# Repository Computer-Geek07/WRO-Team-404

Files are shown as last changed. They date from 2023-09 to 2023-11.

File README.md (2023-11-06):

# Introduction to the team
We are Team 404, a group of three tenth graders from Dhirubhai Ambani International School who are interested in robotics and innovation. We have different roles and skills in our team:

**Arjun**: He is one of our programmers, who works mainly with PID and control algorithms when it comes to the bot. He designed most of the algorithms that go into integrating the sensor feedback and making our bot work precisely as it should.

**Atishaya**: He is another programmer, who works with Arjun to develop and test the robot’s software. He however, focusses mainly on aspects like low-level communication. He worked very hard on the initial code for the open and obstacle categories.

**Meher**: She is our constructor, who designed the mechanical systems of the bot. She specialises in Computer Aided Drawing but managed quite well with the practical construction aspects as well.

# Engineering process

### Programming and electricals
Initially, we were hoping to design our bot, completely devoid of any form of computer vision, relying on a network of colour and proximity sensors for both the open and obstacle categories. However, we very quickly realised that this was if not impossible then at least extremely impractical and switched to a raspberry pi based computer vision system. We looked into various systems and combinations of systems, including ROS to simplify the developmoent process and OpenCV or YOLO or even training our own model for the detection of the traffic signs. Eventually we settled on a combination of ROS to handle hardware coordination and OpenCV to handle object detection. Our openCV program involved masking the image to only read red and green and then running Canny edge detection followed by contour detection to find the traffic signs. Once the traffic signs were found, we would once again run a colour mask to find out whether they were red or green.

We quickly discovered that this process was not only quite difficult to program but it also caused the raspberry pi to become a massive computational bottleneck, slowing down our bot and making it extremely unreliable at high speeds. Looking into alternatives, we discovered HuskyLens, a device designed by DFRobot, that was built to solve exactly the problem we are facing. Switching to the HuskyLens, we added an arduino for low-level hardware communication and for controlling the motors. To this we added an l298N to control our DC motor alongside a DS 35kgcm servo. We also added an MPU6050 and ultrasonics which alongside a PID algorithm helped keep the bot centred on the track and prevent accidents.

After our nationals, we chose to further redesign our bot, we replaced the Arduino Uno with an Arduino Nano Esp32, a smaller and faster board. We also replaced the unreliable HC-SR04s with far more reliable analog ultrasonics from DFRobot, the URM-09s. We also added an ultrasonic in the front of the bot for the obstacle challenge round, where exiting each turn near the centre of the track was of the utmost importance. Our open code was very similar to before, utilizing nearly the same PID algorithm. We were however, forced to completely redesign our obstacle algorithm as it had proven to be unreliable and faulty during the nationals. 

## Construction
While preparing for Nationals, we explored various mechanisms like Ackerman Steering in CAD but eventually decided that most of these were too elaborate for our needs. Our first constructed chassis consisted of a mobile front axle. The wheels were attached to two pivoting parts on either side, which were connected by a servo-controlled link. Our rear axle was fixed and the driving axle in this design. This iteration was bulky and a sharper turn than 35 degrees was practically unfeasible without major slipping which would hinder readings, especially for the IMU. This setup produced an ICR (Instantaneous centre of rotation) and turning radius far too large to fit within the 1m box and made turning a challenge. 

To create a smaller turning radius, we decided to implement all-wheel steering in our next design. We connected our servo to the front and back axles, which were independent of the chassis frame with gears and links. Thus, both front and back axles turned at the same time, in opposite directions, giving the desired narrow ICR. Unfortunately, after extensive testing, we concluded that gear play caused the axles to turn at different angles causing drifting. In the end, our final Nationals robot was front-wheel driven and rear-wheel steering, an alternative that gave us the least slippage and drift.

After the nationals were over, we reworked our bot, using our learning from the nationals to create a simpler, more elegant and far more precise bot.

# Programming

## Open category
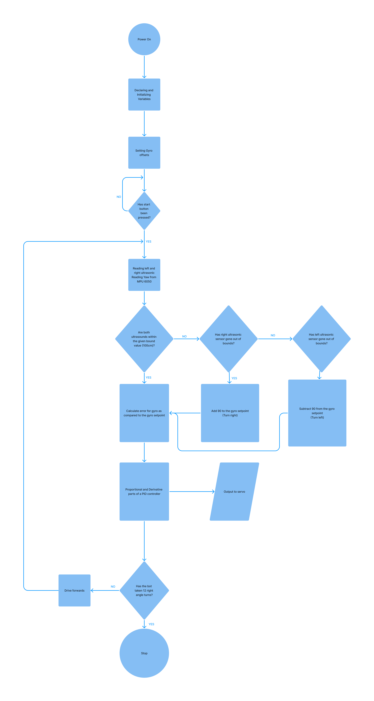
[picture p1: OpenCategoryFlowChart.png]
Open Category Program flowchart Open Category Flow Chart


Our code for the open category runs entirely on an Arduino ESP32 Nano. It receives inputs from various sensors which are combined in a simple PID controller program. For example, we use the yaw value from an MPU6050 to ensure that our bot maintains its heading parallel to the walls. We also take advantage of proximity values from our ultrasonic sensors to detect when the bot has to turn by checking if either of the proximity sensors read a value over 1 meter, which wouldn't be possible in the straight sections of the track. The sensor that has read this high value could only read it if the bot has passed the inner wall and is in a turning section. In this case, we will turn by 90 degrees towards the sensor that has read this high value.

Our bot’s steering is controlled exclusively by our PID controller, even during turns. It takes the yaw value from the Inertial Measurement Unit (MPU6050 in this case) and calculates the error from what the bot's heading should be. This is then run through a standard PID controller, using only the proportional and derivative aspects to calculate the correction the bot will have to make to return to the correct heading. When taking the turns in the corner section of the track, we simply add or subtract 90 degrees from the gyro setpoint, which is the value the PID controller uses to check the bots current heading against.

An issue we faced with turning was that the proximity sensors would read out of bounds multiple times during a single turn, leading to the bot's setpoint being increased by more than the 90 degrees that it should have. We overcame this issue quite simply by ensuring that the bot cannot make two turns within a set period of time, allowing us to create an extremely simple and reliable open code.

## Obstacle Category
After spending some time working with the Raspberry Pi, we decided our obstacle category program would be a lot simpler using an Arduino and some form of Artificially Intelligent Camera like the HuskyLens. Our program at a conceptual level is quite simple. The HuskyLens identifies objects on screen and recognises and categorises them as Red or Green traffic signs. This information is then transmitted to the Arduino, which checks if the sign is on the correct side of the screen. For example, if the traffic sign was red, the bot would make sure it was on the left side of its screen so that the bot passes it on the sign's right. The only real issue we faced with this program was that occasionally the bot would miss traffic signs at turns, if they were outside its Field Of View during the turn. To counteract this, we wrote a script that brings the bot out of the turn, and reverses it, allowing it to read the entire straight section, ensuring we do not miss any traffic signs. The steering and control mechanisms are otherwise almost exactly identical to the Open Category, with a slight distinction being the turning, and the alterations to the PID code to allow the bot to avoid the obstacles.

The way the bot actually avoids the obstacles is by forming a large arc around the obstacles, based on two factors. The distance travelled in the arc, given by the encoder count, and the magnitude of the arc, which is given by the turning angle. The turning angle is calculated as a function of the XCenter (which is the coordinates of the centre of the obstacle on a Cartesian plane, taking the centre of the camera Field of View as 0,0) and then recalculated at every iteration of the main loop as a function of the inverse of the encoder count, i.e., if the encoder count is 0, the turning angle will be maximum. The encoder count is also calculated as a function of the XCenter of the object. Making both the encoder count and the turning angle a function the XCenter of the object allows the bot to make smaller compensations for objects that are already close to where they should be, for example, if there is a red object to the left side of the screen (XCenter is negative), both the encoder count and turning angle will be a lot less, allowing the bot to make a smaller compensation, the reverse of course applies if a red traffic sign is on the right side of the screen. 

## Compiling the code
**Open**
The code for the open category can be used very simply by downloading the relevant .ino files and uploading them to an Arduino Nano ESP32 via the Arduino IDE. This will however also require the installation of the [MPU6050 Light library by rfetick](https://github.com/rfetick/MPU6050_light) alongside the [ESP32 Servo Library by JKB](https://github.com/jkb-git/ESP32Servo) from the arduino IDE library manager, the Wire library being included by default. You will also have to install the package for the Arduino Nano ESP32 as this is not included in the IDE by default. This is of course provided that the you have already constructed a similar bot and done the electricals for the same.

**Obstacle**
The code for the open category can be used very simply by downloading the relevant .ino files and uploading them to an Arduino Nano ESP32 via the Arduino IDE. This will however also require the installation of the [MPU6050 Light library by rfetick](https://github.com/rfetick/MPU6050_light), the [HuskyLens library](https://github.com/HuskyLens/HUSKYLENSArduino) from the given link alongside the [ESP32 Servo Library by JKB](https://github.com/jkb-git/ESP32Servo) from the arduino IDE library manager, the Wire library being included by default. You will also have to install the package for the Arduino Nano ESP32 as this is not included in the IDE by default. One would also have to train the HuskyLens by following the instructions [here](https://wiki.dfrobot.com/HUSKYLENS_V1.0_SKU_SEN0305_SEN0336) and training the HuskyLens to detect multiple colours, tagging Red as 1 and Green as 2. This is of course provided that the you have already constructed a similar bot and done the electricals for the same.

# Electricals
Our bot is based around the following components:
- Arduino Nano ESP32
- HuskyLens
- DS Servo (35kgcm)
- L298N motor driver
- DC-to-DC buck converter
- MPU 6050
- Ultrasonic Sensors - URM09
- Orange Johnson 600 RPM DC motor
- Orange Lithium Polymer Battery 3300, mAh, 11.1 V
- Jumper cables

### Arduino Nano ESP32
The Arduino Nano ESP32 is the brains of our bot, despite being a microcontroller rather than a single board computer like the Raspberry Pi, it is extremely powerful and versatile, able to reliably control our bot even at very high speeds. It takes inputs from the ultrasonic sensors and controls the servo and L298N with its digital pins while communicating over I2C with the MPU6050 and the HuskyLens. The Arduino is powered by a 9V line for one of our DC-to-DC buck converters.

### HuskyLens
The HuskyLens is an easy-to-use Artificially Intelligent camera. It has various built-in features like facial recognition and object tracking. We however chose it for the incredible ease with which it could be programmed to detect and track a traffic light along with outputting its colour. It then communicates the coordinates along with the width and height of this traffic light to our Arduino via I2C. It is powered by a 3.3V line from the Arduino Nano ESP32.

### DS Servo
This servo is controlled by the arduino via a PWM signal on one of its digital pins. The servo rotates to the angle given to it by the arduino and thus steers the bot. It is powered by a DC-to-DC Buck converter that steps the 12V current from the battery down the the 9V more suitable to the servo.

### DC-to-DC buck converter
We are using 2 DC-to-DC buck converters to convert the 12V from the battery into both a 9V connection for the servo, and a 3.3V connection for the sensors and Arduino Nano ESP32.

### L298N motor driver and Orange 600 RPM DC motor
We chose the orange dc motor as it had a high enough torque to move our bot while not being too slow to make a good time as well. Given that we were using a motor of this size, the L298N was the only logical choice.  We control the L298N from three digital pins on the arduino. Two of those pins use high and low signals to determine the direction of the spinning of the motor while the third relies on a PWM pin to set the speed. These get their power directly from the battery as the motor requires 12V. 

### Ultrasonic Sensor (URM-09)
The ultrasonic sensors are placed on either side of the bot, reading the distances from the walls the bot is travelling alongside. This allows us to detect when the bot has to turn, by reading for values over 1 meter. Each ultrasonic sensor shares its readings with the arduino using analog signals to analog in pins on the arduino. These sensors are powered from the 3.3V buck. There is also an Ultrasonic in the front of the bot which is used to indicate when to begin reversing during turning.

### Inertial Measurement Unit (MPU6050)
The MPU6050 is controlled by the Arduino via an I2C connection. The MPU is used to get a yaw value helping us find the current heading of the bot and keep the bot angled correctly. It is powered from the 3.3V buck.
<hr>

## General Purpose Board
We also chose to solder the electronics for the bot onto a General Purpose Board as this would help to eliminate chaotic jumpers and make all the connections more reliable, cleaner and overall just easier to keep track of. This also allowed us to have a common ground for the entire bot. 

<br>
<br>
<br>

# Construction
Our final chassis for the International round is a rear-driven, front-steering module. It consists of an independent front axle connected directly to a servo motor, as well as a differential gearbox on the fixed rear axle. 

The power transmission mechanism from the motor to the rear axle relies simply on the differential gearbox, the coupling such that the wheel with lower traction receives greater power and rotates at higher speeds. Thus, during turning, despite being a fixed axle, our rear will be able to prevent slippage, with the outer wheel rotating faster than the inner. 

The Servo used is the DS-R003B 35Kg Digital Servo , and the DC power motor is the Orange Johnson 12 Volt 600 RPM motor. All mounts and other specialized components are 3D-printed in PLA. The belly pan of the chassis and other supporting components are CNCd and made of polycarbonate.

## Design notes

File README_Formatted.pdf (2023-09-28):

# Team 404

# Team 1076

# Introduction to team

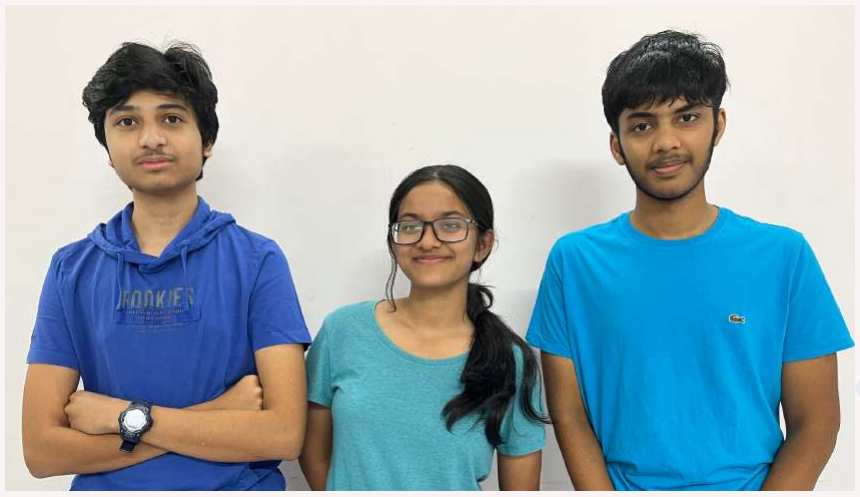
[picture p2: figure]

We are Team 404, a group of three tenth graders from Dhirubhai Ambani International School who are interested in robotics and innovation. We have different roles and skills in our team:

Arjun: He is one of our programmers, who works mainly with PID and control algorithms when it comes to the bot. He designed most of the algorithms that go into integrating the sensor feedback and making our bot work precisely as it should.4

Atishaya: He is another programmer, who works with Arjun to develop and test the robot’s software. He however, focusses mainly on aspects like low-level communication. He worked very hard on the initial code for the open and obstacle categories.

Meher: She is our constructor, who designed the mechanical systems of the bot. She specialises in Computer Aided Drawing but managed quite well with the practical construction aspects as well.

# Engineering process

# Programming and Electricals

Initially, we were hoping to design our bot, completely devoid of any form of computer vision, relying on a network of colour and proximity sensors for both the open and obstacle categories. However, we very quickly realised that this was if not impossible then at least extremely impractical and switched to a raspberry pi based computer vision system. We looked into various systems and combinations of systems, including ROS to simplify the developmoent process and OpenCV or YOLO or even training our own model for the detection of the traffic signs. Eventually we settled on a combination of ROS to handle hardware coordination and OpenCV to handle object detection. Our openCV program involved masking the image to only read red and green and then running Canny edge detection followed by contour detection to find the traffic signs. Once the traffic signs were found, we would once again run a colour mask to find out whether they were red or green.

We quickly discovered that this process was not only quite difficult to program but it also caused the raspberry pi to become a massive computational bottleneck, slowing down our bot and making it extremely unreliable at high speeds. Looking into alternatives, we discovered HuskyLens, a device designed by DFRobot, that was built to solve exactly the problem we are facing. Switching to the HuskyLens, we added an arduino for low-level hardware communication and for controlling the motors. To this we added an l298N to control our DC motor alongside a DS 35kgcm servo. We also added an MPU6050 and ultrasonics which alongside a PID algorithm helped keep the bot centred on the track and prevent accidents.

# Construction Process

Our first chassis consisted of a mobile front axle connected to two links which were further attached to extrusions that formed the main frame of the robot. They were connected at a single pivot point, allowing the links to move back and forth, pulling the axle with it. The servo motor was initially attached to just one of these links. The overall transmission of power began with the servo moving one of the links left or right, which in turn pulled the shaft and other links left or right. Our rear axle remained the driving axle and was not connected to the servo in this design. While we wished to connect the second, non-powered link to the rear axle, we realized that would pull both axles in the same direction, which opposed the desired result. Further, this iteration was bulky and had a huge Instantaneous Center of Rotation (ICR), as a result, we first sought to make it more sophisticated in version 2.

In our second version of the chassis, we decided to replace the 4-bar linkage system with a single, 3-D printed Servo-controlled link, which would in turn, transmit power to two 3-D Printed pivoting parts on the extrusion frame of the chassis to which the wheels were attached using bearings. This version was much smaller and more reliable than the last, however, it did consume valuable space that could have been used for housing electronic components. Further, this setup, much like the last, was a front-wheel steering and rear-wheel powered setup. Since a sharper turn than 40 degrees practically is unfeasible without major slipping, this setup still produced an ICR far too large to fit within the 1m box and made turning a challenge.

# Construction Process

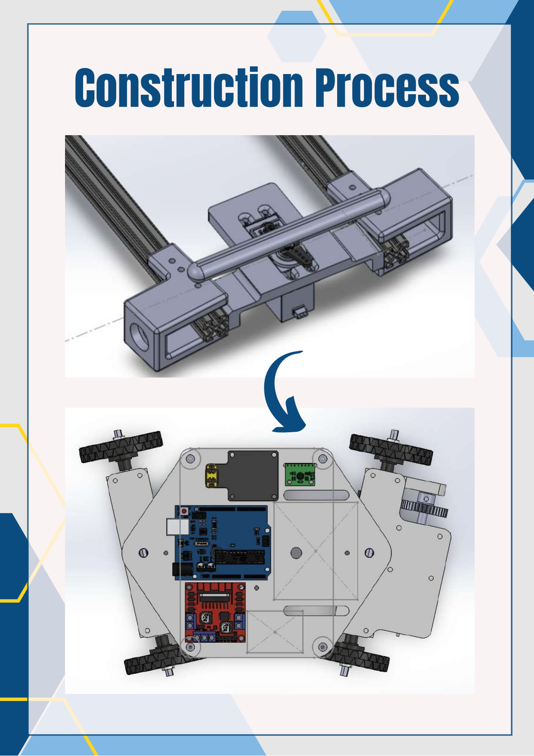
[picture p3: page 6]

# Programming

# 0pen Challenge

Our code for the open category runs entirely on an Arduino Uno. The Arduino receives inputs from various sensors for various purposes. These are combined in a simple PID controller program. We use the yaw value from an MPU6050 to ensure that our bot maintains its heading parallel to the walls, while we use the left and right proximity values from ultrasonic sensors to prevent the bot from getting too close to the walls.

We also take advantage of these proximity values to detect when the bot has to turn by checking if either of the proximity sensors read a value over a meter, which wouldn't be possible in the straight sections of the track. The sensor that has read this high value could only read it if the bot has passed the inner wall and is in a turning section. In this case, we will turn by 90 degrees towards the sensor that has read this high value.

Our bots steering is controlled by our PID controller. It takes the values from the Inertial Measurement Unit and the ultrasonic sensors and calculates the error from what the bot's heading should be. These are then multiplied with their respective gains to give a form of weightage to the sensors inputs, with the ultrasonic gain being inversely proportional to the IMU's error. These are then run through a standard PID controller, using only the proportional and derivative aspects to calculate the correction the bot will have to make to return to the correct heading.

After spending some time working with the Raspberry Pi, we decided our obstacle category program would be a lot simpler using an Arduino and some form of Artificially Intelligent Camera like the HuskyLens. Our program at a conceptual level is quite simple. The HuskyLens identifies objects on screen and recognises and categorises them as Red or Green traffic signs. This information is then transmitted to the Arduino, which checks if the sign is on the correct side of the screen. For example, if the traffic sign was red, the bot would make sure it was on the left side of its screen so that the bot passes it on the sign's right.

The only real issue we faced with this program was that occasionally the bot would miss traffic signs at turns, if they were outside its Field Of View during the turn. To counteract this, we wrote a script that brings the bot out of the turn, and reverses it, allowing it to read the entire straight section, ensuring we do not miss any traffic signs. The steering and control mechanisms are otherwise

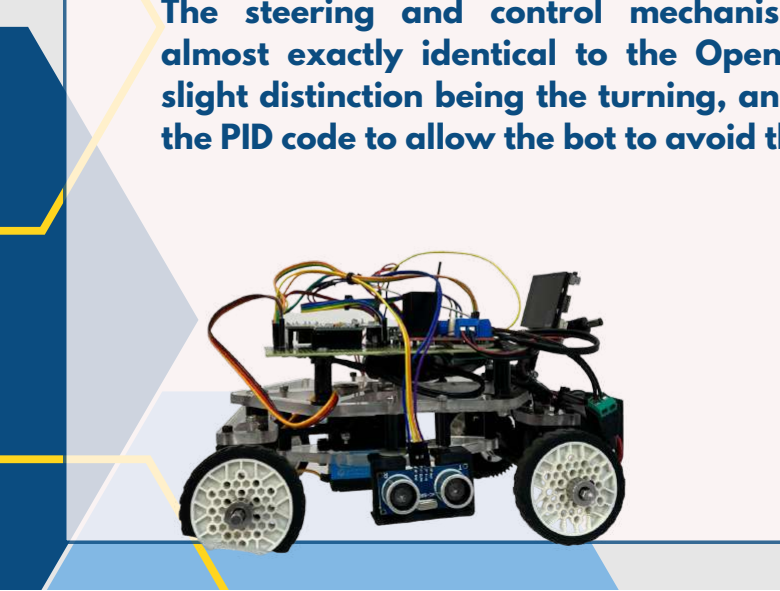
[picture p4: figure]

almost exactly identical to the Open Category, with a slight distinction being the turning, and the alterations to the PID code to allow the bot to avoid the obstacles.

# Obstacle Challenge

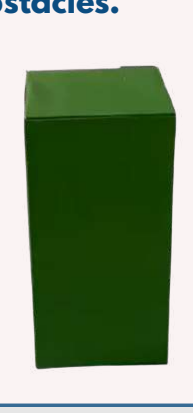
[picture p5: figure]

Open The code for the open category can be used very simply by downloading the relevant .ino files and uploading them to an Arduino Uno via the Arduino IDE. This will however also require the installation of the MPU6050 Light library by rfetick from the arduino IDE library manager, the Wire and Servo libraries being included by default. This is of course provided that the you have already constructed a similar bot and done the electricals for the same.

Obstacle The code for the obstacle category can be used very simply by downloading the relevant .ino files and uploading them to an Arduino Uno via the Arduino IDE. This will however also require the installation of the MPU6050 Light library by rfetick from the arduino IDE library manager and the HuskyLens library from the given link, the Wire and Servo libraries being included by default. One would also have to train the HuskyLens by following the instructions here and training the HuskyLens to detect multiple colours, tagging Green as 1 and Red as 2. This is of course provided that the you have already constructed a similar bot and done the electricals for the same.

# Compiling the code

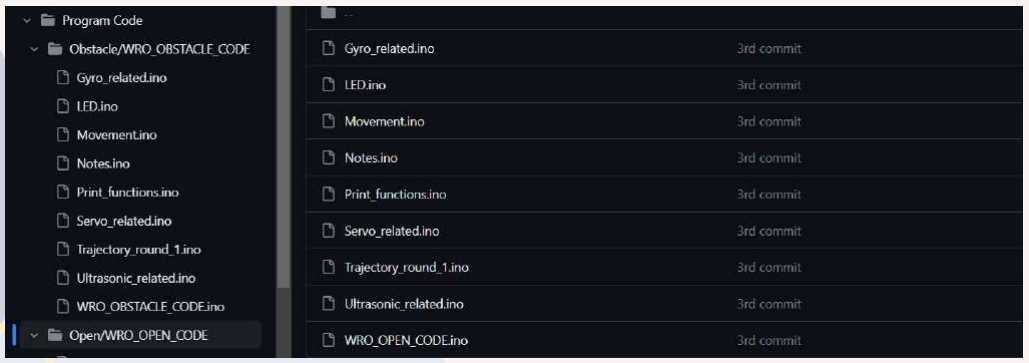
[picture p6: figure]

# Electricals

# Electro-mechanical Components

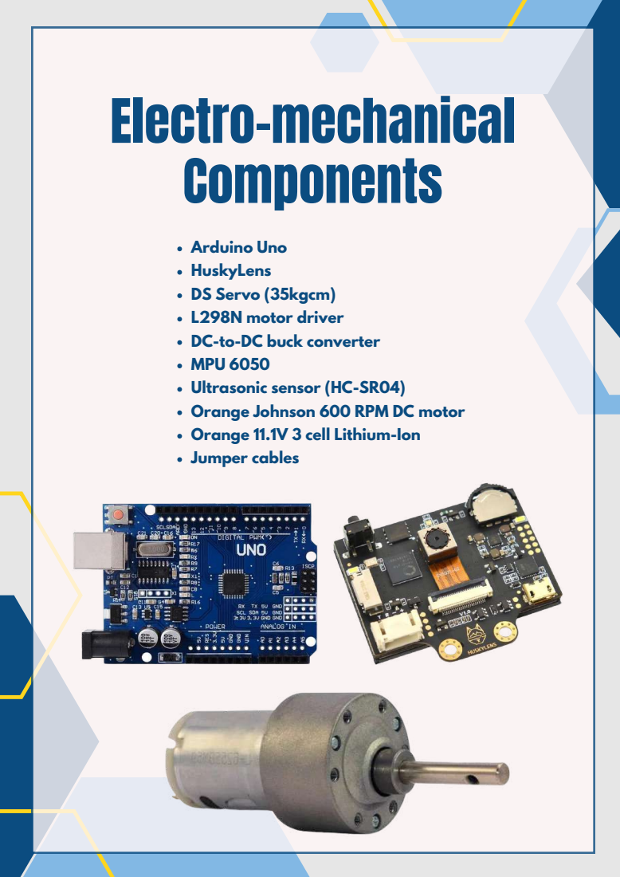
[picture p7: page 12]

Arduino Uno
HuskyLens
DS Servo (35kgcm)
L298N motor driver
DC-to-DC buck converter
MPU 6050
Ultrasonic sensor (HC-SR04)
Orange Johnson 600 RPM DC motor
Orange 11.1V 3 cell Lithium-Ion
Jumper cables

# Electrical Components

Arduino Uno: The Arduino Uno is the brains of our bot, despite being a microcontroller rather than a single board computer like the raspberry pi, it is extremely powerful and versatile, able to reliably control our bot even at very high speeds. It takes inputs from the ultrasonic sensors and controls the servo and L298N with its digital pins while communicating over I2C with the MPU6050 and the HuskyLens. The Arduino is powered by a 5V line from the L298N.

HuskyLens: An easy-to-use Artificially Intelligent camera. It has various built in features like facial recognition and object tracking. We however chose it for the incredible ease with which it could be programmed to detect and track a traffic light along with outputting its colour. It then communicates, the coordinates along with the width and height of this traffic light to our arduino via I2C. It is powered by the 5V line from the L298N.

DS Servo and Buck Converter: This servo is controlled by the arduino via a PWM signal on one of its digital pins. The servo rotates to the angle given to it by the arduino and thus steers the bot. It is powered by a DC-to-DC Buck converter that steps the 12V current from the battery down the the 7.2V more suitable to the servo.

# Electrical Components

Orange Johnson 600 RPM DC motor and L298N: We chose the orange DC motor as it had a high enough torque to move our bot while not being too slow to make a good time as well. Given that we were using a motor of this size, the L298N was the only logical choice. We control the L298N from three digital pins on the Arduino. Two of those pins use high and low signals to determine the direction of the spinning of the motor while the third relies on a PWM pin to set the speed. These get their power directly from the battery as the motor requires 12V. The L298N also outputs 5V power that we use to power our Arduino and various sensors

Ultrasonic Sensor - HC SR 04: The ultrasonic sensors are placed on either side of the bot, reading the distances from the walls the bot is travelling alongside. This allows us to maintain our bot along a straight heading and prevents it from getting too close to the walls. Each ultrasonic sensor is controlled by the Arduino via 2 digital pins. The trigger and echo pins. The Arduino operates them by sending a pulse on the trigger pin and then measuring the length of the returned pulse on the echo pin. These sensors are powered by the 5V line from the L298N.

MPU 6050: The MPU6050 is controlled by the Arduino via an I2C connection. The MPU is used to get a yaw value helping us find the current heading of the bot and keep the bot angled correctly. It is powered by the 5V line from the L298N.

# Electrical Components

GPB: We also chose to solder the electronics for the bot onto a General Purpose Board as this would help to eliminate chaotic jumpers and make all the connections more reliable, cleaner and overall just easier to keep track of. This also allowed us to have a common ground for the entire bot.

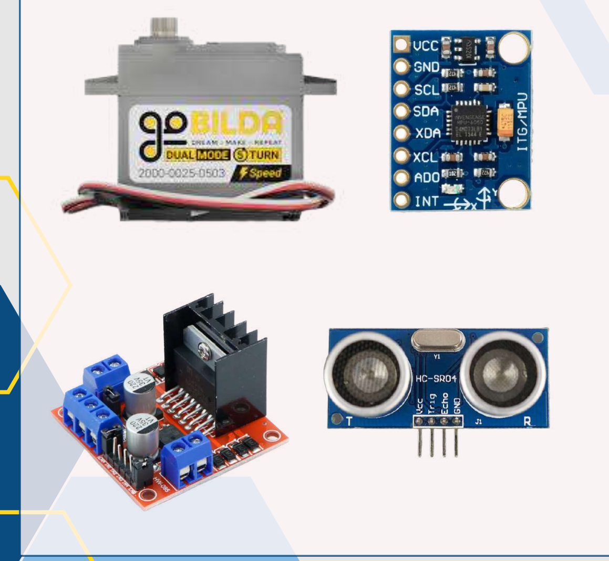
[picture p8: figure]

# Construction

# The Final Design

As mentioned previously, our chassis designs had begun with inspiration from Ackermann Steering, which unfortunately failed for us in the CAD stage. However, during our research period, we found another mechanism that implemented all-wheel steering using a scissor mechanism. While that design was difficult to implement as it would require splitting or chassis in half, we drew inspiration from the same and decided to implement a similar steering to fix our problem of having a too-large ICR. Placing our servo motor beneath our chassis, we connected it to the independent front and back axles initially with links. However, this too, failed in the design phase as the bot would drift large distances.

Thus, we attached on top of our servo, a gear. The gear was then connected with a pair of links each to the front and back axle, which are both independent of the main chassis frame. Thus, both front and back axles turned at the same time, in opposite directions, giving the desired narrow ICR. Unfortunately, after extensive testing, we concluded that the two axles were not turning at the same angles, making the turning unreliable. To combat the issue, we removed a gear and set of links from the front axle, making it a rear-steering bot.
We concluded in testing that there was lesser slippage and drift with the front wheels being powered. Thus, overall, the front and back axles are independent of the main chassis body, with the front axle powered, and the back axle steering.
The power transmission mechanism on the front wheels is simple, two gears, one on the wheel axis and the other on the motor were coupled, hence generating motion.
All links, gears and other specialized components are 3D-printed in PLA. The belly pan of the chassis and other supporting components were made using a CNC machine out of polycarbonate.

# The Final Design

# The Front

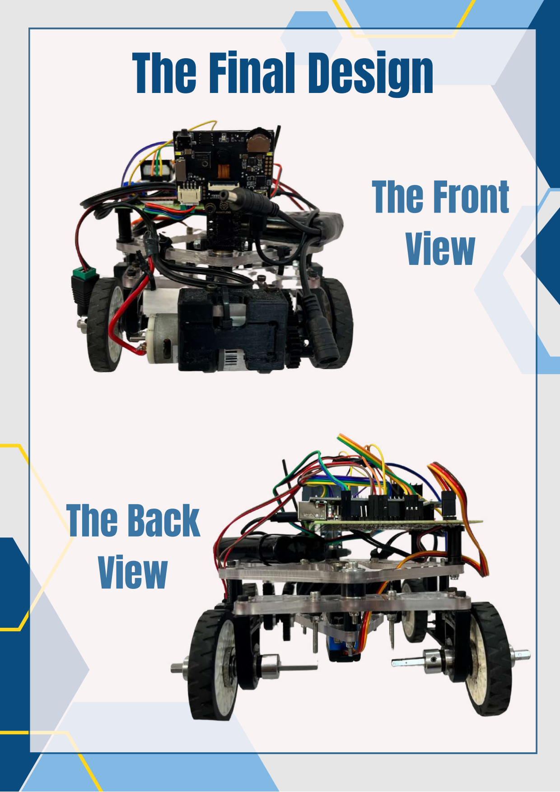
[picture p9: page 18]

# View

# The Back View

# The Final Design

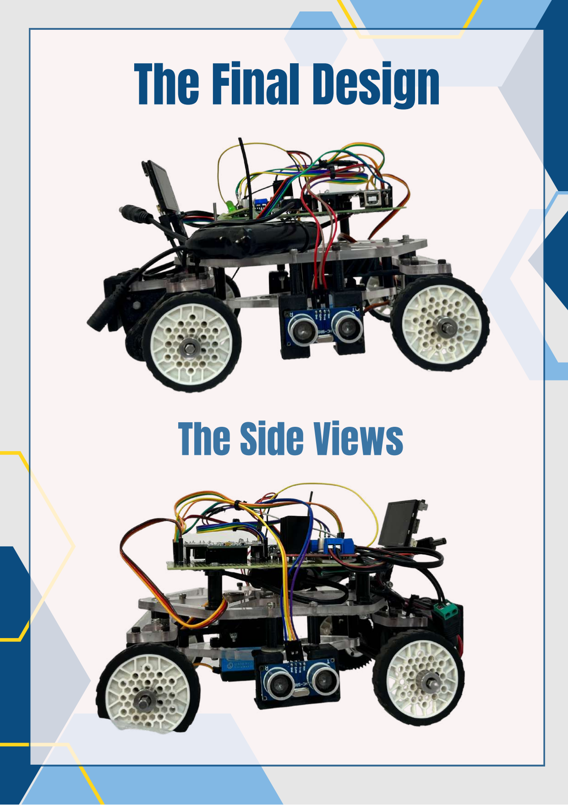
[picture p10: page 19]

# The Side Views

# The Final Design

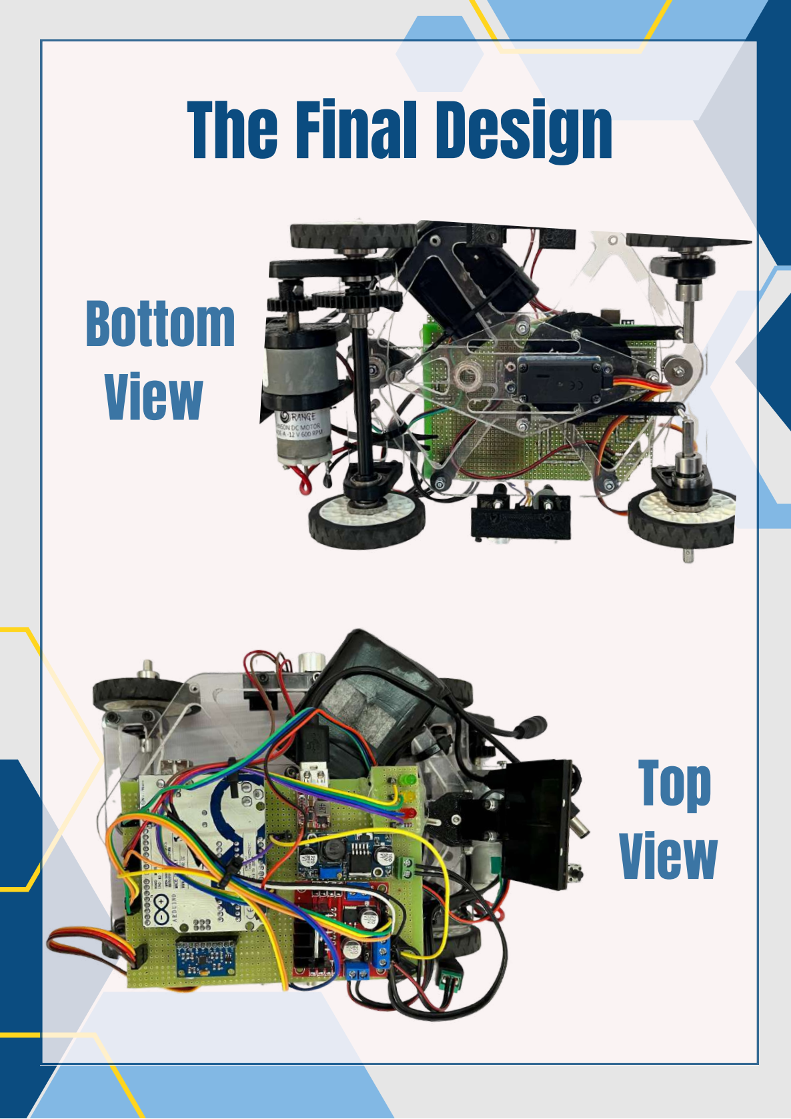
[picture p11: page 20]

# Bottom View

# Top View

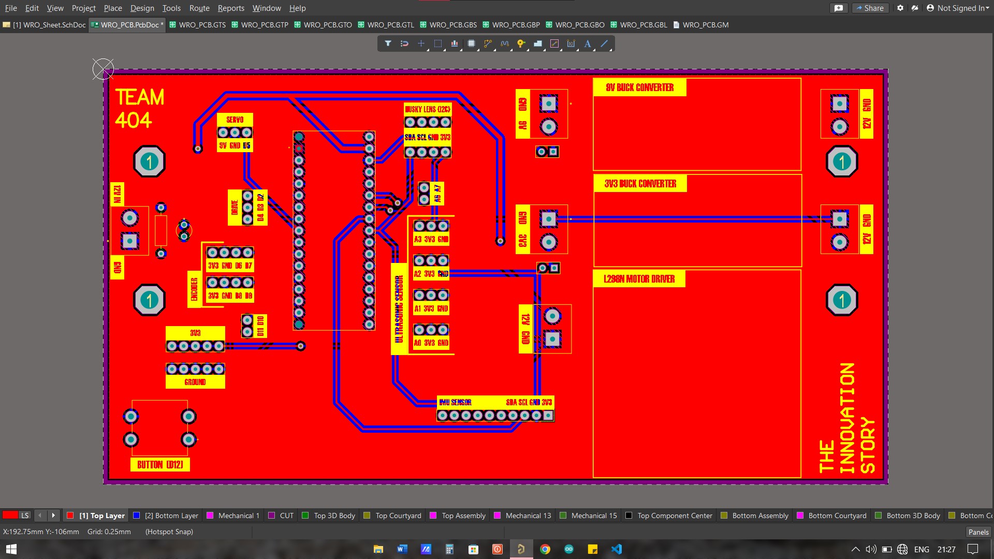
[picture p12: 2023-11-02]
WRO_GPB_Design.jpg

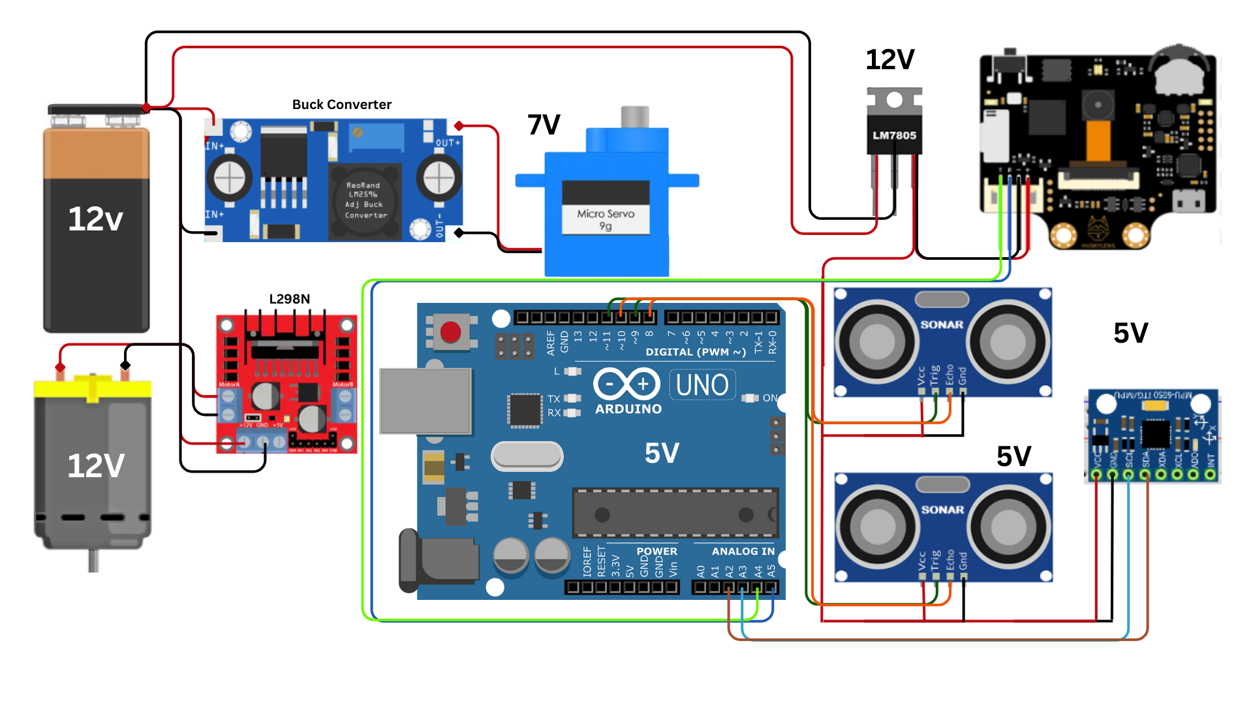
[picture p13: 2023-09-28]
Circuit Diagram.png

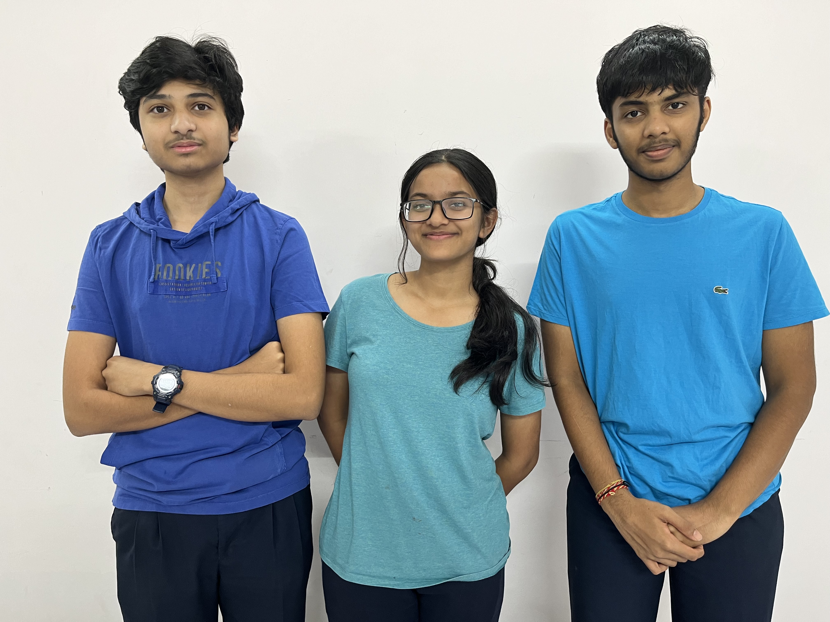
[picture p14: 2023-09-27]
TeamPhoto.jpg

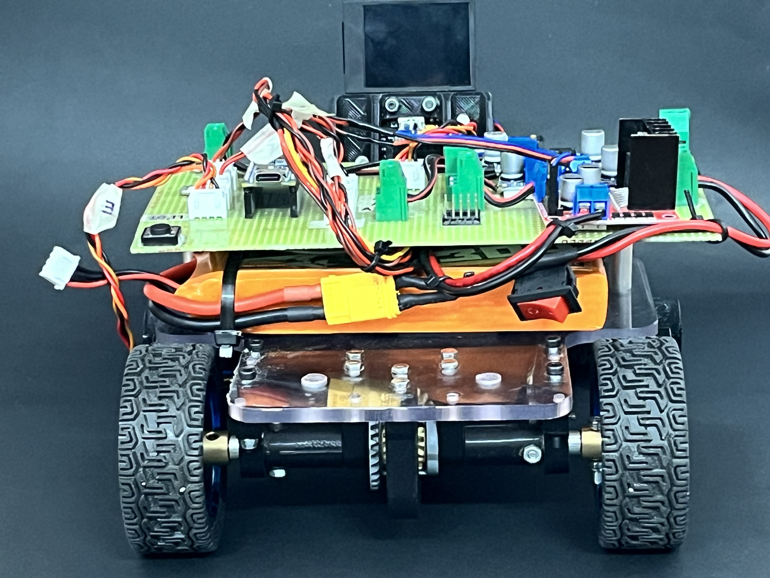
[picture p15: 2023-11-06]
404 Bot Photos/Bot Back.jpg

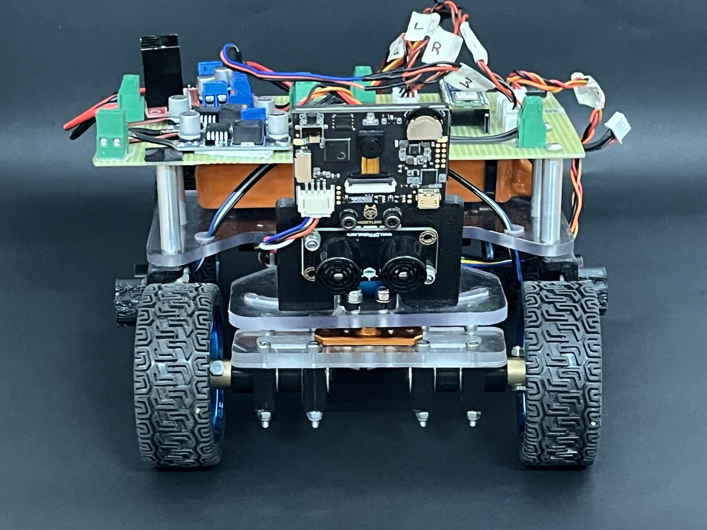
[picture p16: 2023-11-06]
404 Bot Photos/Bot Front.jpg

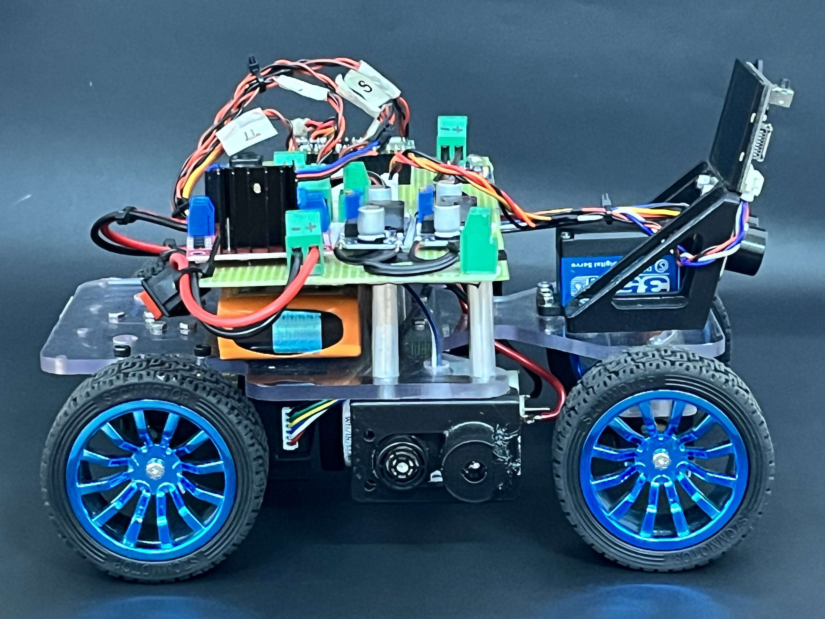
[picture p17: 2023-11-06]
404 Bot Photos/Bot Left.jpg

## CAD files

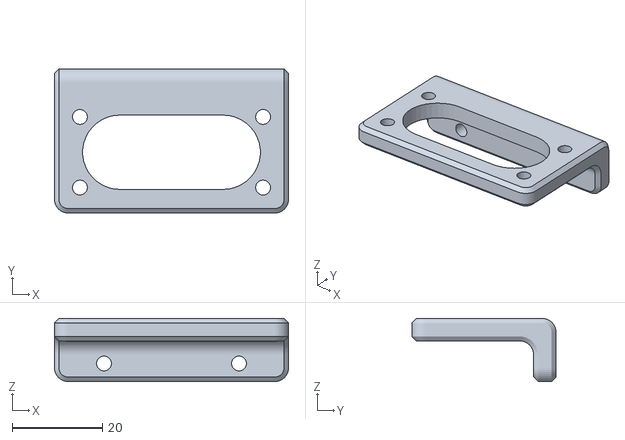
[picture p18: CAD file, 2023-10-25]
Construction/3D print parts/umr09 holder.STL
52.0 x 32.0 x 14.0

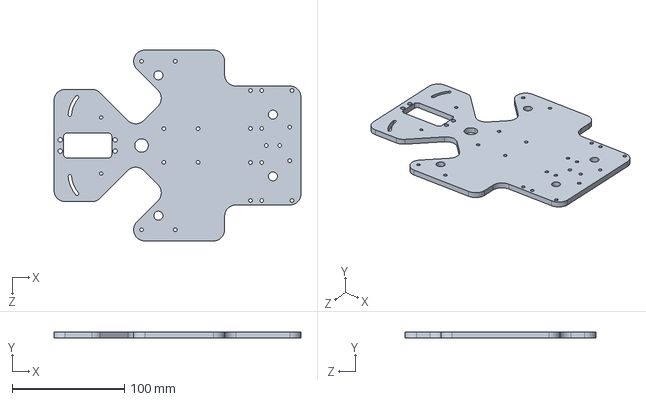
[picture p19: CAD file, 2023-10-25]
Construction/CNC Parts/chassis bod.STEP
220.0 x 5.00 x 170.0 mm

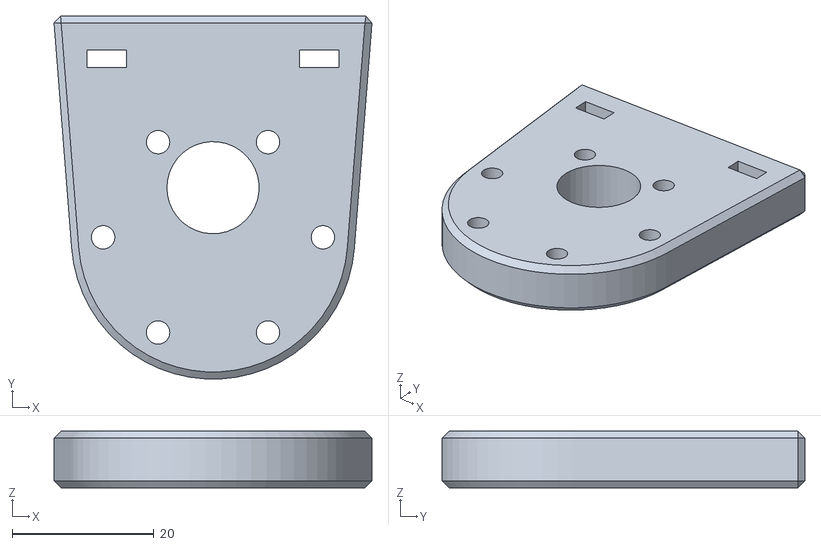
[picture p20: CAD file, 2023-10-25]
Construction/3D print parts/motor plate new.STL
44.8 x 51.2 x 8.00

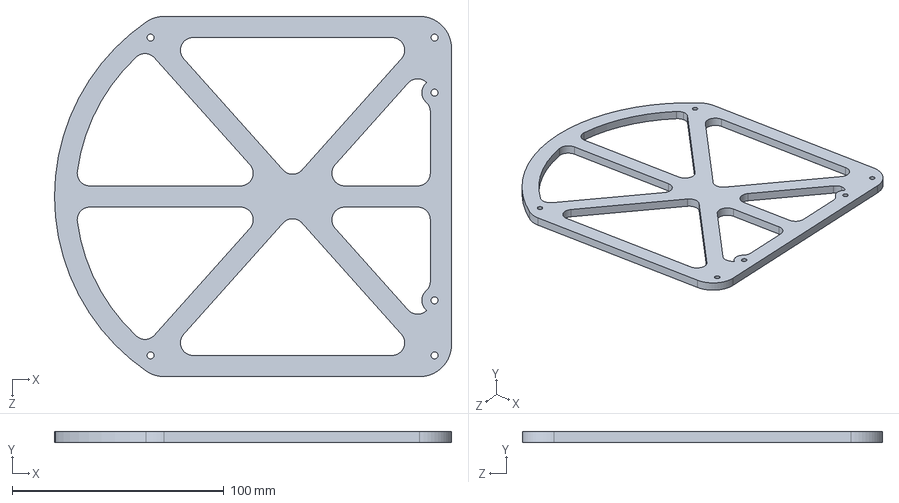
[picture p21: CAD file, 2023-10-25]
Construction/CNC Parts/upper plate.STEP
187.3 x 5.00 x 170.0 mm

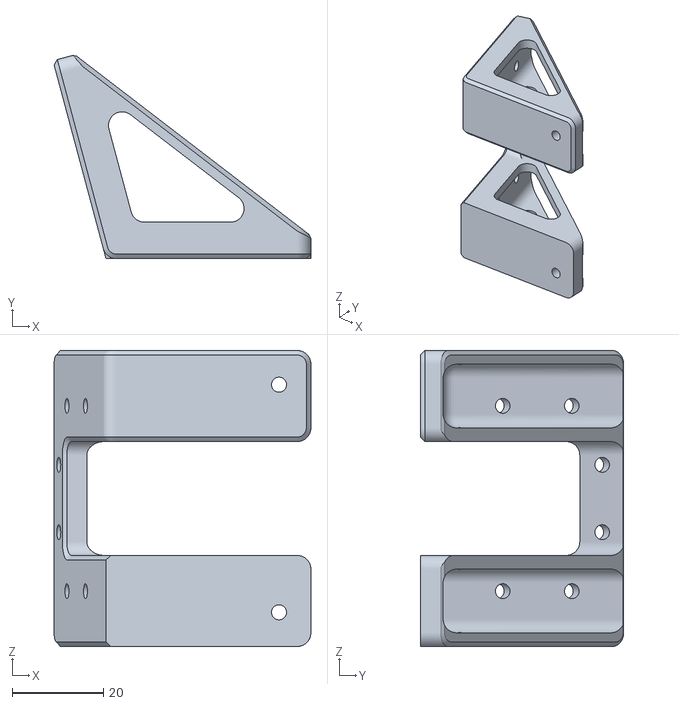
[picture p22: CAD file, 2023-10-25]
Construction/3D print parts/husky mount straight.STL
56.4 x 44.6 x 65.0

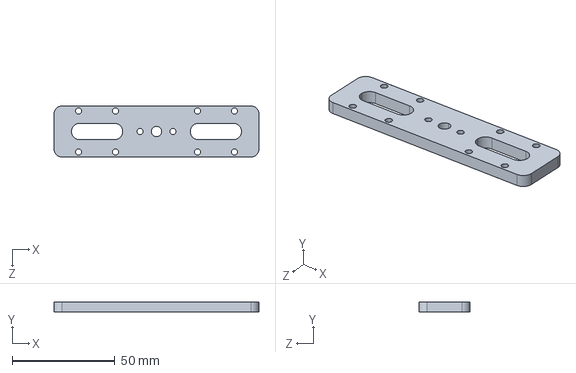
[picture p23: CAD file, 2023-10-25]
Construction/CNC Parts/front axel support.STEP
100.0 x 5.00 x 25.0 mm

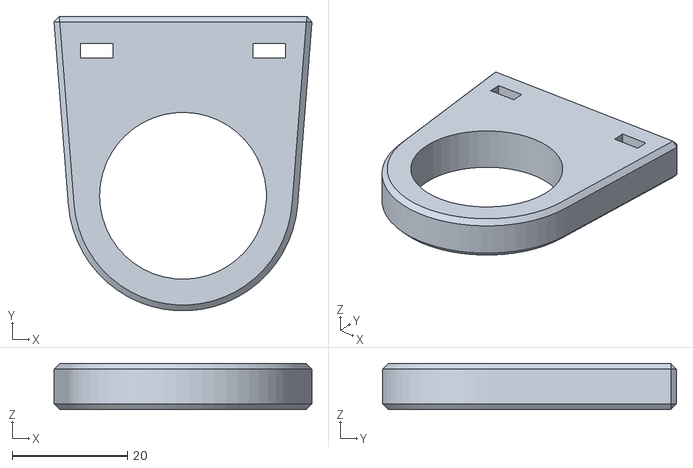
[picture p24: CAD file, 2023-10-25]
Construction/3D print parts/motor plate new back.STL
44.8 x 51.2 x 8.00

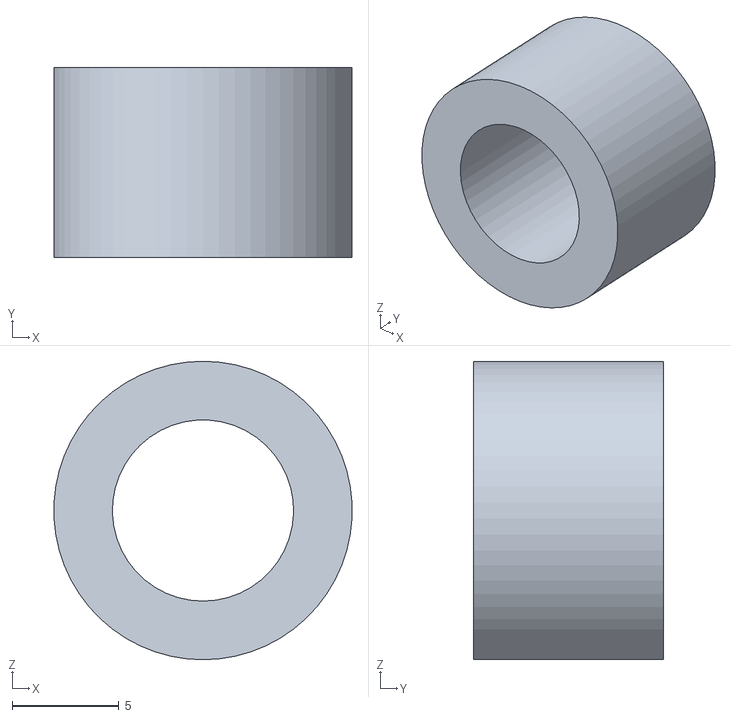
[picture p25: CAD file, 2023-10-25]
Construction/3D print parts/shaft bearing spacer.STL
14.0 x 8.90 x 14.0

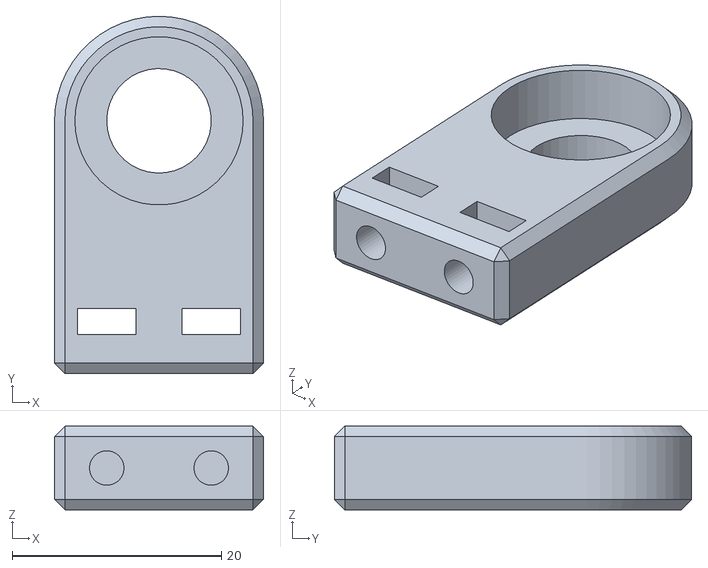
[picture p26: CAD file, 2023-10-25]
Construction/3D print parts/6_12_holder long.STL
20.0 x 34.2 x 8.00

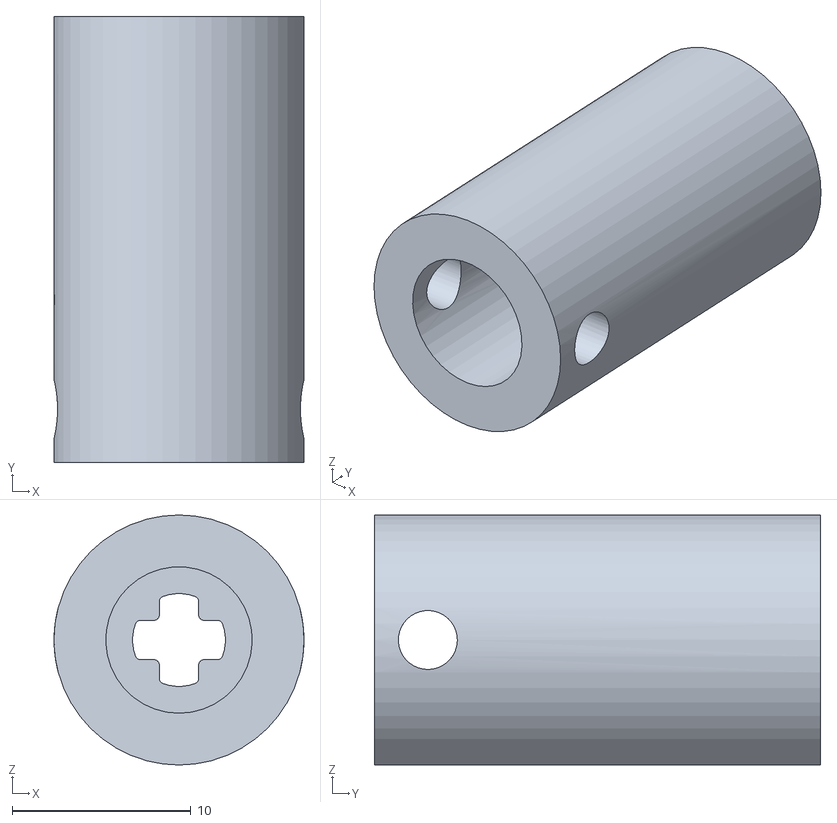
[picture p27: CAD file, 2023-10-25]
Construction/3D print parts/axel to actual axel.STL
14.0 x 25.0 x 14.0

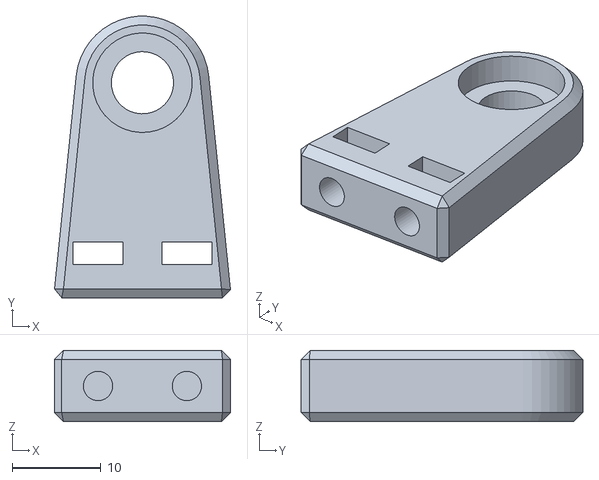
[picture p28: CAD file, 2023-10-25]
Construction/3D print parts/5_11_holder.STL
19.8 x 31.7 x 8.00

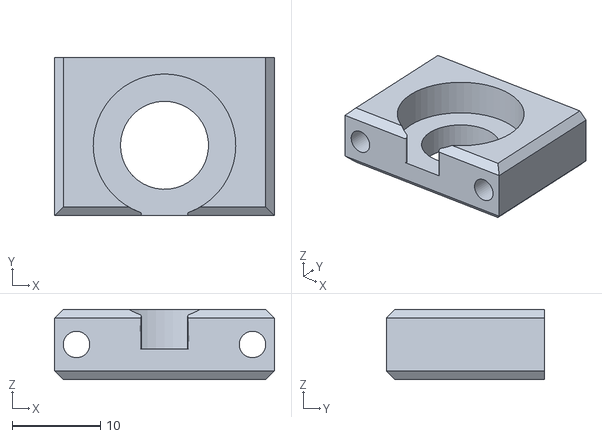
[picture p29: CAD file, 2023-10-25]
Construction/3D print parts/6_12_holder.STL
25.0 x 18.0 x 8.00

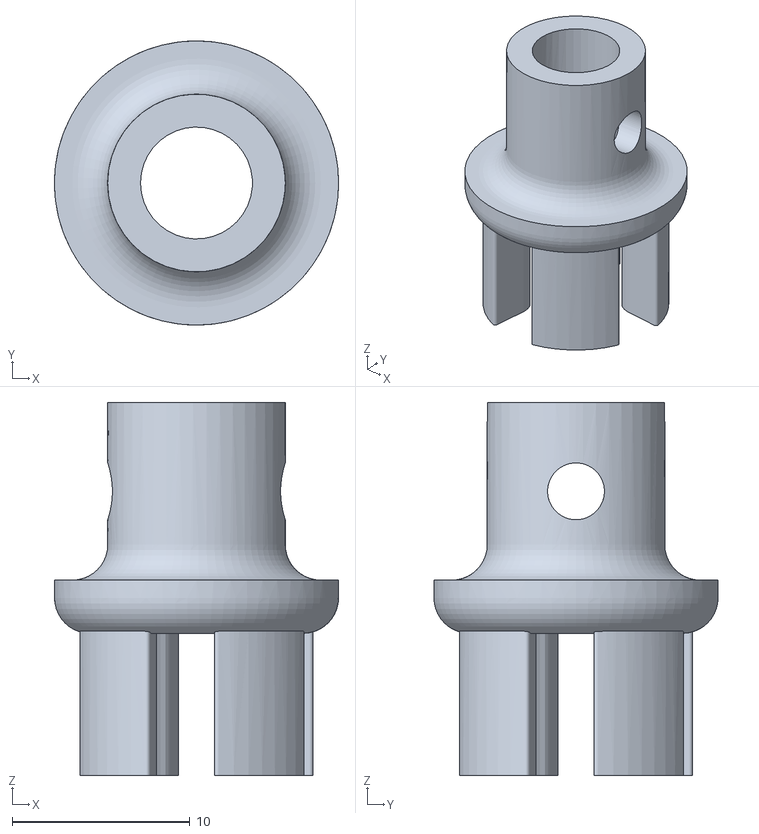
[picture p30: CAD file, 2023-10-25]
Construction/3D print parts/on lego to motor.STL
16.0 x 16.0 x 21.0

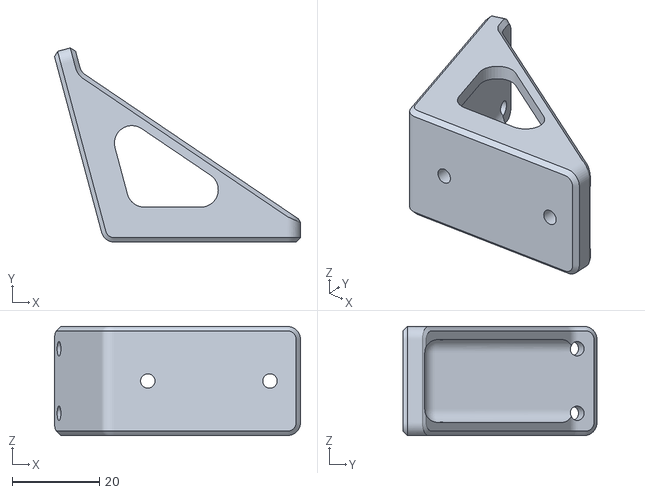
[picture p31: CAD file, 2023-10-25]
Construction/3D print parts/husky mount angle.STL
56.4 x 44.5 x 25.0

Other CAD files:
Construction/3D print parts/differential support.STL

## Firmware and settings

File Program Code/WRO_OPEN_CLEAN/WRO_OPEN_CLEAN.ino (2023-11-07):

// #include <Servo.h>
#include <ESP32Servo.h> 
#include "Wire.h"
#include <MPU6050_light.h>
#include <NewPing.h>
#include "WiFi.h"

// LED Pins
#define greenLED 15
#define yellowLED 13
#define redLED 14
#define blueLED 16

// //Gyro-related variables
MPU6050 mpu(Wire);
int currentAngle;

//Ultrasonic pin declarations
const int triggerPinLeft = A1;   // Analog output pin for the first ultrasonic sensor
const int triggerPinRight = A2;  // Analog output pn for the second ultrasonic sensor

//Ultrasonic ops variables
float distanceRight;
float prevDistanceRight;
float distanceLeft;
float prevDistanceLeft;
int OOBThresh = 110;
int OOB = 0;

//Servo variables
#define servo_pin 5
Servo servoMotor;
int prevAngle = -1;

//Motor declarations
const int enaPin = 4;  // Enable pin
const int in1Pin = 3;  // IN1 pin
const int in2Pin = 2;  // IN2 pin
int prevPower = -1;
float motorSpeed = 100;

//Gyro PID variables
float error_gyro = 0;
int setPoint_gyro = 0;
int setPoint_flag = 0;

//Effective gyro PID variables
float kp = 6;  // Proportional gain
float kd = 0.5;  // Derivative gain
float ki = 0.0;
float prevErrorGyro = 0.0;
float correction = 0.0;
float totalErrorGyro = 0.0;

float error_ultrasonic = 0.0;
float totalErrorUltrasonic = 0.0;
float prevErrorUltrasonic = 0.0;


// //Turn related variables
int leftTurn = 0;
int rightTurn = 0;
int counter = 0;
unsigned long startTime;

unsigned long prevMillis;

void setup() {
  // put your setup code here, to run once:
  Serial.begin(9600);
  Wire.begin();

  //motor setup
  pinMode(enaPin, OUTPUT);
  pinMode(in1Pin, OUTPUT);
  pinMode(in2Pin, OUTPUT);

  //led setup
  pinMode(greenLED, OUTPUT);
  pinMode(redLED, OUTPUT);
  pinMode(yellowLED, OUTPUT);

  //ultrasonic setup
  pinMode(triggerPinRight, INPUT);
  pinMode(triggerPinLeft, INPUT);
  prevDistanceRight = readDistanceNew(triggerPinRight);
  prevDistanceLeft = readDistanceNew(triggerPinLeft);

  //servo setup
  servoMotor.attach(servo_pin);
  servoMotor.write(91);

  //mpu setup
  byte status = mpu.begin();
  Serial.print(F("MPU6050 status: "));
  Serial.println(status);
  while (status != 0) {}  // stop everything if could not connect to MPU6050
  Serial.println(F("Calculating offsets, do not move MPU6050"));
  delay(1000);
  mpu.calcOffsets();  // gyro and accelero
  Serial.println("Done!\n");
  prevMillis = millis();

  // Wifi disabling
  WiFi.disconnect(true);
  WiFi.mode(WIFI_OFF);

  // Start button
  // Readiness indicated by yellow LED (pin 13)
  pinMode(12, INPUT_PULLUP);
  pinMode(13, OUTPUT);
  while (digitalRead(12) == HIGH) {
    Serial.println("Button not pressed");
    digitalWrite(13, HIGH);
  }
}

void loop() {
  // put your main code here, to run repeatedly:

  // Check for ultrasounds being Out of Bounds
  ultrasounds();

  // Read angle from gyro
  currentAngle = getAngle();

  // Stop after 3 rounds
  if (counter >= 12 && (OOB == 0)) {
    drive(0);
  } 
  else {
    drive(motorSpeed);
  }

  // If one of the ultrasonics has gone out of bounds
  if (OOB == 1) {
    // The bot is allowed to turn
    if (setPoint_flag == 0) {
      startTime = millis();

      // Turn in the relevant direction, left or right
      if (leftTurn == 1 && rightTurn == 0) {
        setPoint_gyro = setPoint_gyro + 90;  //change later for the relevant directions
      } else if (rightTurn == 1 && leftTurn == 0) {
        setPoint_gyro = setPoint_gyro - 90;
      }

      // increment turns count
      counter = counter + 1;

      // Stop the bot from turning again
      setPoint_flag = 1;
    }

    // Run gyro PID
    correctAngle(setPoint_gyro);
  } else {

    correctAngle(setPoint_gyro);  //gyro PID
    prevMillis = millis();
  }
  
  // Allow the bot to turn again is 1 second has elapsed since the last turn
  if ((millis() - startTime) > 1000) {
    setPoint_flag = 0;
  }
  }

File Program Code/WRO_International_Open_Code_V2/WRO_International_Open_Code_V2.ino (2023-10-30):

// #include <Servo.h>
#include <ESP32Servo.h> 
#include "Wire.h"
#include <MPU6050_light.h>

// //Gyro-related variables
MPU6050 mpu(Wire);
int currentAngle;

//Ultrasonic pin declarations
const int triggerPinLeft = A7;   // Analog output pin for the first ultrasonic sensor
const int echoPinLeft = 8;       // Analog input pin for the first ultrasonic sensor
const int triggerPinRight = A6;  // Analog output pn for the second ultrasonic sensor
const int echoPinRight = 10;     // Analog input pin for the second ultrasonic sensor

//Ultrasonic ops variables
float distanceRight;
float prevDistanceRight;
float distanceLeft;
float prevDistanceLeft;
int ultrasoundRightOOB = 0;
int ultrasoundLeftOOB = 0;
int OOBThresh = 110;
int OOB = 0;
// int postTurnFlag = 0;

//Servo variables
Servo servoMotor;
int prevAngle = -1;

//Motor declarations
const int enaPin = 3;  // Enable pin
const int in1Pin = 2;  // IN1 pin
const int in2Pin = 4;  // IN2 pin
int prevPower = -1;
float motorSpeed = 150;

//Gyro PID variables
float error_gyro = 0;
// float gyro_gain = 1;
int setPoint_gyro = 0;
int setPoint_flag = 0;

// //Ultrasonic PID variables
// float error_us = 0;
// float ultrasound_gain = 0;

//Effective PID variables
float kp = 6;  // Proportional gain
float kd = 0;  // Derivative gain
float ki = 0.0;
float prevErrorGyro = 0.0;
float correction = 0.0;
float totalErrorGyro = 0.0;

float kp_us = 10;  // Proportional gain
float kd_us = 0;  // Derivative gain
float ki_us = 0.0;

float error_ultrasonic = 0.0;
float totalErrorUltrasonic = 0.0;
float prevErrorUltrasonic = 0.0;


// //Turn related variables
// int usHasRunRight = 0, usHasRunLeft = 0;
// int lastRunTime = 0;
int leftTurn = 0;
int rightTurn = 0;
int counter = 0;
unsigned long startTime;
// unsigned long startTimeTurn;
// unsigned long startTimeForward;
// int startTimeTurnFlag = 0;
// int startTimeForwardFlag = 0;

// LED Pins
int greenLED = A0;
int yellowLED = A1;
int redLED = A2;

unsigned long prevMillis;
void setup() {
  // put your setup code here, to run once:
  Serial.begin(9600);
  Wire.begin();

  //motor setup
  pinMode(enaPin, OUTPUT);
  pinMode(in1Pin, OUTPUT);
  pinMode(in2Pin, OUTPUT);

  //led setup
  pinMode(greenLED, OUTPUT);
  pinMode(redLED, OUTPUT);
  pinMode(yellowLED, OUTPUT);

  //ultrasonic setup
  // pinMode(triggerPinRight, OUTPUT);
  pinMode(echoPinRight, INPUT);
  // pinMode(triggerPinLeft, OUTPUT);
  pinMode(echoPinLeft, INPUT);
  prevDistanceRight = readDistanceNew(triggerPinRight);
  prevDistanceLeft = readDistanceNew(triggerPinLeft);

  //servo setup
  servoMotor.attach(11);
  servoMotor.write(91);

  //mpu setup
  byte status = mpu.begin();
  Serial.print(F("MPU6050 status: "));
  Serial.println(status);
  while (status != 0) {}  // stop everything if could not connect to MPU6050
  Serial.println(F("Calculating offsets, do not move MPU6050"));
  delay(1000);
  // mpu.upsideDownMounting = true; // uncomment this line if the MPU6050 is mounted upside-down
  mpu.calcOffsets();  // gyro and accelero
  Serial.println("Done!\n");
  prevMillis = millis();
  // drive(motorSpeed);
}

void noloop(){
  ultrasounds();
}

void loop() {
  // put your main code here, to run repeatedly:
  //800 millis for oob1

  ultrasounds();

  // printDistance();
  currentAngle = getAngle();
  if (counter >= 12 && (OOB == 0)) {
    drive(0);
  } 
  else {
    drive(motorSpeed);
  }

  // if (ultrasoundRightOOB == 0 && ultrasoundLeftOOB == 0) {
  //   OOB = 0;
  //   digitalWrite(greenLED, LOW);
  // } else {
  //   OOB = 1;
  //   digitalWrite(greenLED, HIGH);
  // }

  if (OOB == 1) {
    if (setPoint_flag == 0) {
      startTime = millis();
      if (leftTurn == 1 && rightTurn == 0) {
        setPoint_gyro = setPoint_gyro + 90;  //change later for the relevant directions
      } else if (rightTurn == 1 && leftTurn == 0) {
        setPoint_gyro = setPoint_gyro - 90;
      }
      counter = counter + 1;
      // digitalWrite(yellowLED, LOW);
      setPoint_flag = 1;
    }
    // turn(95 - 90);
    // delay(800);
    // turn(95);
    // delay(200);
    correctAngle(setPoint_gyro);
    // pid_us(setPoint_gyro, distanceLeft,40,false);
    // Serial.println("Out of bounds");
  } else {
    // setPoint_flag = 0;
    // turn(95);
    // if(millis()-prevMillis >= 50){
    correctAngle(setPoint_gyro);  //eventually PID
    // pid_us(setPoint_gyro, distanceLeft,40,false);
    prevMillis = millis();
    // }
    // Serial.println(correction);
  }
  
  if ((millis() - startTime) > 1000) {
    // digitalWrite(yellowLED, HIGH);
    setPoint_flag = 0;
  }
  
  // Serial.println(setPoint_gyro);
}

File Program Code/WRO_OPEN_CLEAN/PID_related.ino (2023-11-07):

// Gyro PID
void correctAngle(float setPoint_gyro) {
  error_gyro = currentAngle - setPoint_gyro;

  float pTerm = 0;
  float dTerm = 0;
  float iTerm = 0;

  pTerm = kp * error_gyro;
  dTerm = kd * (error_gyro - prevErrorGyro);
  totalErrorGyro += error_gyro;
  iTerm = ki * totalErrorGyro;

  correction = pTerm + iTerm + dTerm;

  // If the bot is not turning
  // Limit the correction to 5 degrees
  // To prevent oscillations
  if (setPoint_flag == 0) {
    if (correction > 5) {
      correction = 5;
    } else if (correction < -5) {
      correction = -5;
    }
  } else { //  If bot is turning, increase the steering range
    if (correction > 35) {
      correction = 35;
    } else if (correction < -35) {
      correction = -35;
    }
  }

  prevErrorGyro = error_gyro;
  turn(90 + correction);
}

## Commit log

2023-09-24 Added manufacturing files
    [8.3 mm Spacer.STL, Body wro.STEP, Motor Body mount Plate.STL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]
2023-09-28 Circuit diagram upload
2023-10-25 3D print part files for updated bot
    [5_11_holder.STL, 6_12_holder long.STL, 6_12_holder.STL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]
2023-10-25 Added CNC files for updated bot
    [chassis bod.STEP, front axel support.STEP, upper plate.STEP]
2023-10-30 Updated Open Code
    Split ultrasonic and gyro pid into two separate programs
2023-11-06 Updated compiling instructions for the ESP32 based board
2023-11-06 Updated Open Category Flowchart
2023-11-06 Updated the Open Category Flow Chart
2023-11-06 Uploaded the updated open category flowchart
